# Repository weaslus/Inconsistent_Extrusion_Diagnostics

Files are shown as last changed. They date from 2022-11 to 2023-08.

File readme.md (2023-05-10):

Prints look like this?

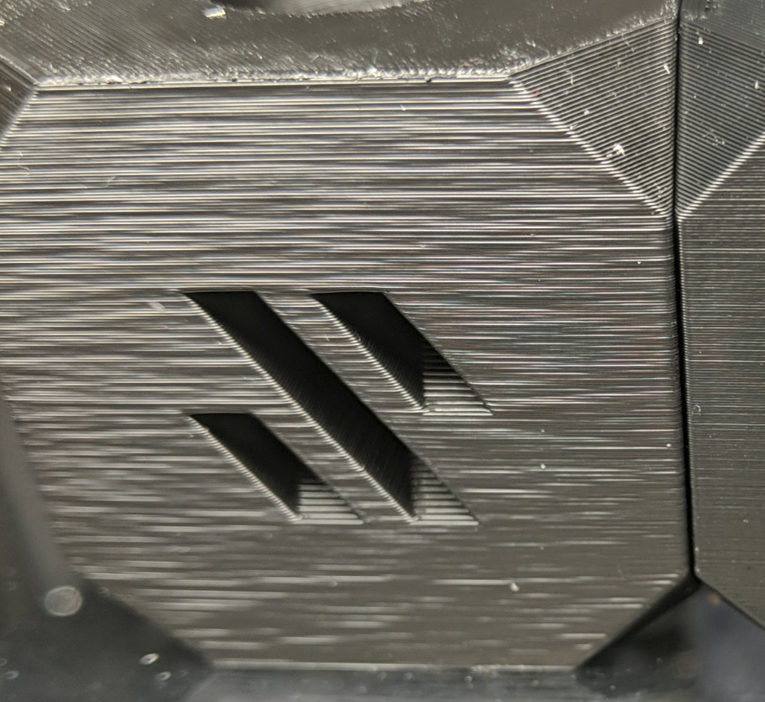
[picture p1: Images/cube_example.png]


This tool aims to help diagnose the source of the issue. I'll leave the theory till... yes. I'll begin with a walkthrough.
# Setting Expectations

Please do not think, after running this test, and a small adjustment, you will have perfect even walls. Often that is just not possible. I hope people are using this to find the cause of unuseually large and unsightly issues. If you are studying every part with harsh angled light, stop it.
# Step By Step
1) Download the Reducing_Tower found in STLs folder, inspired by Mihai Designs.

2) Slicer settings: This needs to be printed in vase mode, (or spiralise outer contour for cura) with no infil, and 1 wall. 
A 0.2 LH and 0.6 LW are recommended. Keep comfortable below your flow rate limit.

Those using SuperSlicer: Please make sure to input the layer width value in the left column, not the right hand "line spacing" column.

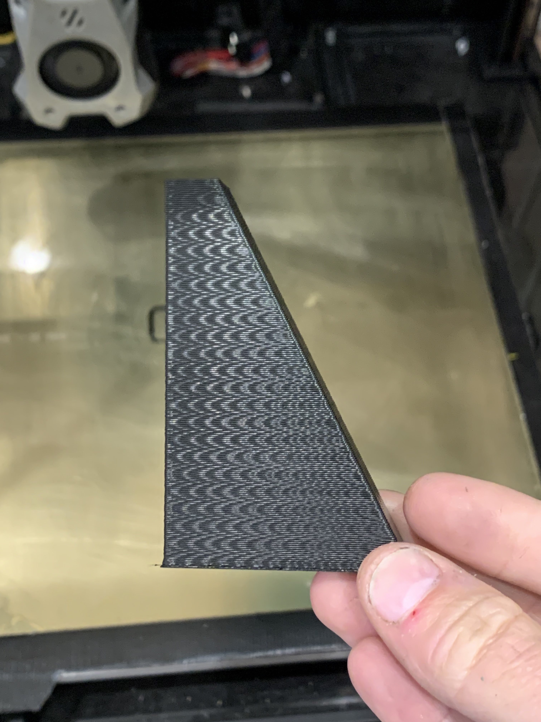
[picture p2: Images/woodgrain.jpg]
woodgrain


3) Once printed, you should be able to see some woodgrain, as per the above example photo (maybe not as pronounced). We are interested in the length of the repeat of this grain effect. The easiest place to measure, would be tip to tip of the grains, as pictured.

For increased accuracy: you may measure over multiple repeats of the pattern, if possible, and divide by the number of gaps you span. Accuracy is vital here. The difference between patters caused by your motor backlash (on a bmg), and your idler tension, is very small. This is also why i recommend a finer layer height and line width than Mihai. It will stretch the patterns and make them more distinct. Calipers are strongly recommended for this task.

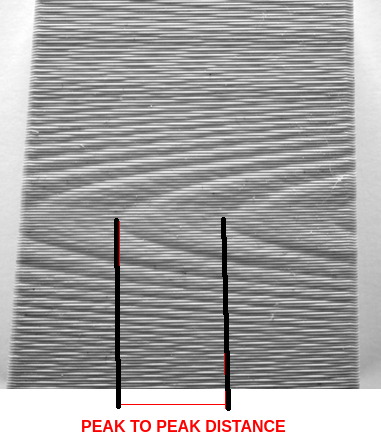
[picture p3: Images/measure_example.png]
Measure this


If you see a virtical band, and not woodgrain, proceed to #large format.

4) Enter the peak to peak measurment, into the document [here](https://docs.google.com/spreadsheets/d/1iBX4ItWAsnH7RxIQfogGv_I9tm8Rc8wFJSg-SmeD-WY/edit?usp=sharing)
under the "pattern wave length" field, along with your chosen layer height, line width, and slicer used.
Please enter your rotation distance from your printer.cfg. The accuracy of this value does not effect this test. If you are not using klipper, you can calculate this value from esteps, using the formula [found in klipper docs.](https://www.klipper3d.org/Rotation_Distance.html?h=rotation#calibrating-rotation_distance-on-extruders)

5) The value created in red, should be a close match to one of the values in the tables below.
Given the comparison, with any luck, you now know which gear, or interaction, is causing your inconsistency. A close mechanical inspection, and adjustment, should be able to rectify this.

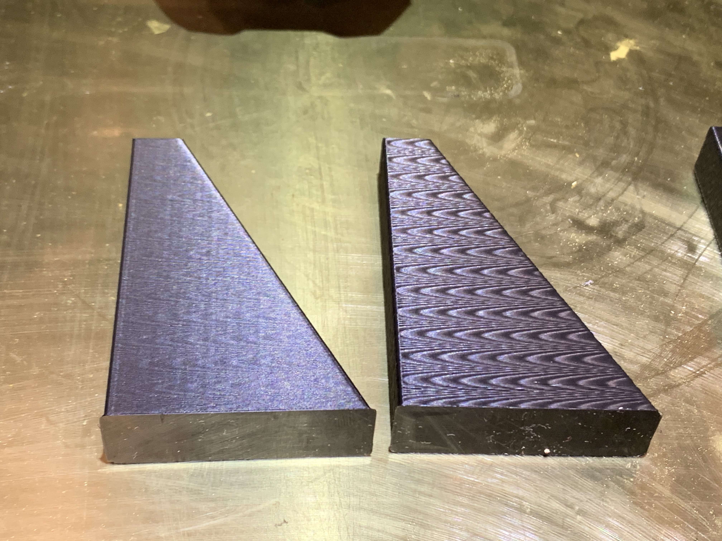
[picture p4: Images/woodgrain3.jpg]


# Large Format

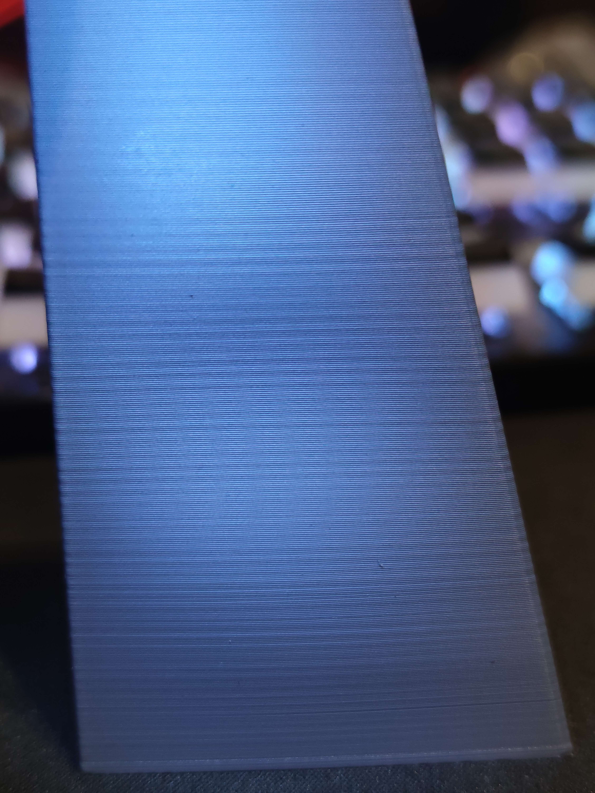
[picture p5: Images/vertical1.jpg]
vertical_example


 For a vertical banding, this indicates very large values between cycles of flow rates. I would suggest printing a simple cylinder in vase mode, of 20mm in diameter and 100-150mm tall. Take note of how much filament the slicer says this will use (volumetric). Make sure to turn off skirts for this value, and any bottom layers; we want a value for the vase portion only. Then you can turn those features back on to print.

 Once printed. You can count the number of cycles. And you know the volumetric flow used to print the tower. Enter these in the appropriate boxes to the right of the spreadsheet and compare to the values below. Guessing at a fractional value, like 4.25 repeats, may increase accuracy.

vertical_example

Currently only BMG gears are directly supported, but please contact me, Weaslus on the voron design or annex engineering discords, if you have other extruders and want help interpreting your results.

# Theory
Words, what are they...
section in progress.

# Thanks
Obviously, the biggest thank you to Mihai Design for pioneering this test print. It has been the inspiration for this tool since the day i first saw it.
I also like to give a shoutout to Foof on the voron discord for creating the initial spreadsheet, and Mazor for just generally being a legend and patient with my and my Github struggles.
Credit to ikeliketocreate from for some beatiful example images.

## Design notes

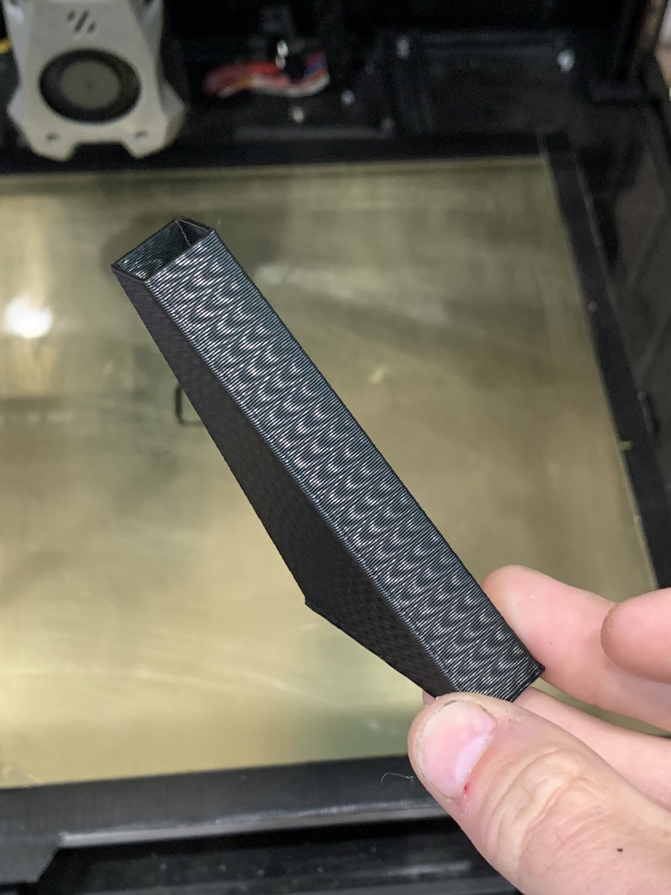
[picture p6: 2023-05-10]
Images/woodgrain2.jpg

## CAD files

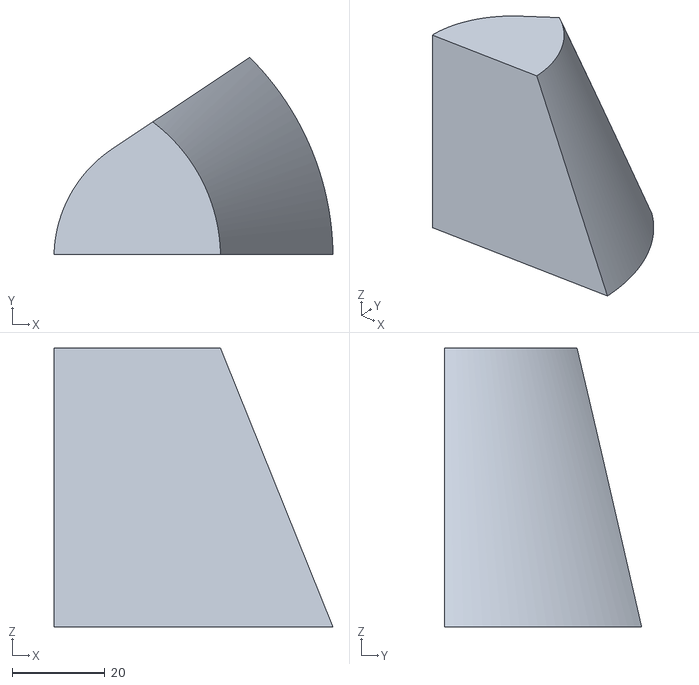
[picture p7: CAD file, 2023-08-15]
STLs/Reducing_Tower.stl
60.0 x 42.4 x 60.0

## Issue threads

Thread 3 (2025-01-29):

Large format test description inconsistency

Kekht, 2025-01-29:
Hi.

In description for Large Format there are said "Take note of how much filament the slicer says this will use (volumetric)" - first of all that is not clear, suppose you meant volume in mm3. Also spreadsheet says "Volumetric Flow", and that is actually not just volume, but volume/time. Sample value (100) without units also distracts, because while using recommended 0.2*0.6 perimeter of 20mm*100mm cylinder it is about 4k mm3 of filament.

Hope you can fix that so it became more clear.

BR,
Kekht
